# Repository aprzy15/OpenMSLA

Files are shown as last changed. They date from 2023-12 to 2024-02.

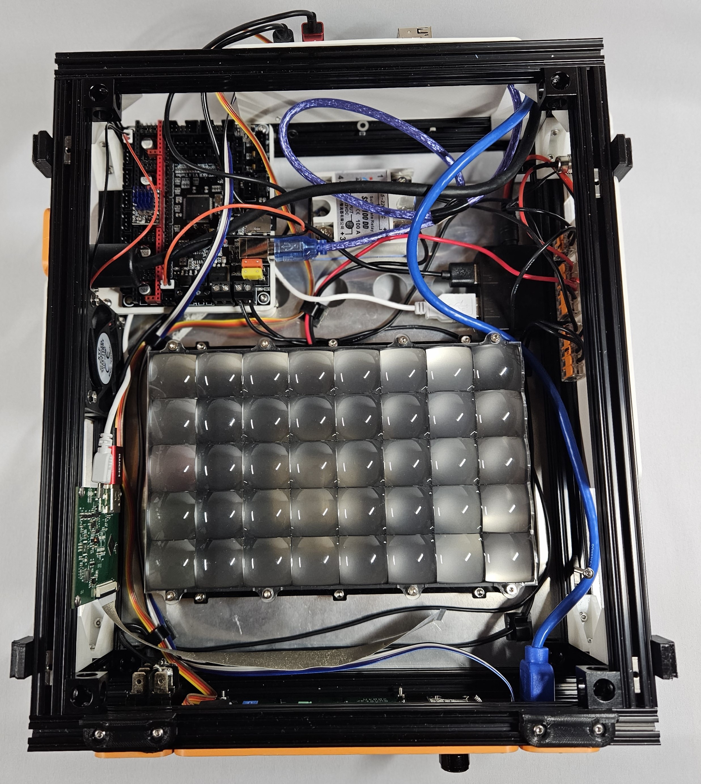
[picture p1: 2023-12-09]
hardware/photos/20231204_174026.jpg

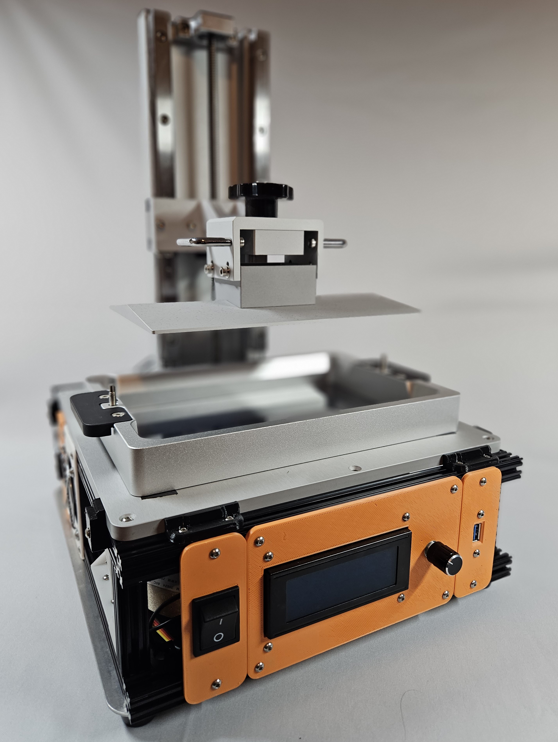
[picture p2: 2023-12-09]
hardware/photos/20231204_174818.jpg

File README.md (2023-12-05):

# OpenMSLA
Open-source resin 3D printer based on masked stereolithography (MSLA) technology

<p align="center" width="100%">
    
</p>

## Purpose

The purpose of the OpenMSLA project is to build an open-source, Python controlled 3D printer that provides operators with an extremely high level of control over printer operation.

## Why?

- As opposed to FDM 3D printing where there is a wide offering of open source 3D printers, almost all commercially available resin printers are closed source.
- Nearly all MSLA resin printers operate on a macro based architecture where machine parameters are defined on a layerwise basis and these parameters are duplicated for use in every subsequent layer.
  - This does not allow the operate to customize printing parameters beyond very basic settings.

## Objective

The objective of this project is to build a Gcode controlled resin printer that in principle will operate much more like an FDM 3D printer. Using this familiar interface should incentivize adoption and provide machine operators with an extremely high level of control over printing parameters of their printer.

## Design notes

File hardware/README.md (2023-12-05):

# Hardware Overview

### Donor Printer
The majority of the printer mechanical components are salvaged from a Phrozen Sonic Mighty 4K. At ~$400 the Sonic Mighty strikes a good balance between cost, quality and size. The LCD base plate, Z actuation arm, build plate, vat, and LED array are salvaged from the Sonic Mighty for use in this project. Unfortuately the LCD that comes with the Sonic mighty directly connects to the main control board via a MIPI cable. Due to the cloased source nature of the Phrozen control board running Chitubox firmware, reverse engineering the communication protocol between the board and the LCD mask would be a significant effort. The easier route is to purchase a new LCD mask off the shelf along with a dedicated LCD driver that allows for connection to a host PC over HDMI.

### Electrical Block Diagram

<p align="center" width="100%">
    
</p>

The OpenMSLA printer uses a Raspberry Pi which runs that main control software. The Pi interfaces with an SKR v1.4 Turbo control board running a flavor of Marlin to control the position of the Z axis actuator and the LCD driver board to display images to the LCD mask. The 24V LED curing array is controlled by a spare 5V fan PWM port on the SKR board via the solid state relay. The printer can be operated remotely over a local network or directly through the user interface mounted on the front of the printer which consists of a character LCD display and an encoder wheel for user input. One of the Pi's usb ports is exposed on the front panel to allow for insertion of a USB drive.

### TODO
- Covers need to be extended around the perimeter of the frame to prevent light bleed from the LED curing array.
- Make rear cover for the Raspberry Pi
- Cable management :)

<p align="center" width="100%">
    
</p>

<p align="center" width="100%">
    
</p>

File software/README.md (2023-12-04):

## OpenMSLA File Spec
The MSLA file is a zip folder with the .zip extension renamed to .msla
The MSLA file contains three main things:
- printconfig.ini file
- printplan.gcode file
- Collection of enumerated PNG files

### printconfig.ini
The print config file contains general information for the build: filename, number of layers, layer height, date time, material info, etc.
As of 11/18/2023 only the number of layers variable is actually used by the machine. The rest of the variables are mainly for record keeping purposes.

### printplan.gcode
The gcode file contains all of the commands for producing the build. This gcode is intended to be sent to a control board running Marlin. There are the following customizations to allow for the board to be used for resin printing purposes:
- ```M106 P0 S[0-255]```
	- The ```P0``` fan port is used to controller the solid state relay which controls power to the LED array. A value of 0 closes the relay, 255 opens the relay. Despite being a PWM port, this command can only be used to fully close or fully open the relay. Therefore only values of 0 and 255 should be used.
- ```M118 R1 I1```
		- ```M118``` is a standard Marlin M command that sends a serial message back to the host computer (in this case the Raspberry Pi). In this case the control board sends the command ```R1 I1``` back to the host. ```R``` Designates that this is a host command to be executed on the host computer. ```R1``` is the host command to display an image to the LCD. ```I1``` designates the index of the image to show. In this case the 1st image is displayed.
## OpenMSLA Gcode command architecture
An MSLA printer requires precise timing of image exposure and light exposure to accurately print parts. In the case of this machine, the image exposure is controlled by the host computer and timing of the LED array is controlled by the Gcode controller. This architecture necessitates precise timing between the host computer and Gcode controller.

When the Gcode controller is sent a Gcode command, this command is stored in an internal buffer until it is ready to be executed. When this internal buffer is filled the  controller will cease to accept new commands. This means that while the host computer knows precisely when a command is sent to the control board, it is "blind" as to when the command is actually executed. This introduces complications when trying to precisely time the display of layer to the LCD with the exposure by the LED array.

When Gcode controller is send a Gcode command, the host will wait until either a response is received or the timeout limit is reached. For most standard gcode commands the host waits for the ```ok``` response. For ```M118``` commands the host will wait for the specified serial message to be received, stalling the sending of gcode commands until this response is received.

The solution to this timing issue is to have the control board be the orchestrator during the print to control the timing of the LED array as well as the LCD. Because the LCD is controlled from the host computer this requires that the control board issue a command to the host computer when it wants a specific image to be displayed. Hence the ```M118 R1 I1``` command described above.

Based on these rules the typical layer is organized like the following:
```
G0 Z1 F500
M118 R1 I1
M400
M106 P0 S255
G4 P500
M106 P0 S0
```
- ```G0 Z1 F500``` Moves the Z axis to a specified Z height at a specified feed rate
	- This command is typically a set of multiple Z commands that control the peeling process and setting the next layer position
- ```M118 R1 I1``` This command issues the host command to display an image
- ```M400``` This command waits for all previously issues gcode commands to finish. In the case of long Z moves, this command is necessary to make sure the Z axis is in the correct position prior to turning on the LED array.
- ```M106 P0 S55``` Turns on the LED array
- ```G4 P500``` Is a 500ms dwell time. This dictates the curing time given for the resin
- ```M106 P0 S0``` Turns of the LED array
It is unclear what the actual timing of the LED array compared the designated dwell time. It is assumed that control board executes commands fast enough that the actual time the LED array is on it not significantly different from the commanded dwell time.

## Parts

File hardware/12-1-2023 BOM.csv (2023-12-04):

name | Manufacturer | vendor | package qty | order qty | price | total price | description | link
15x15x300mm Al extrusion | MakerBeam | MakerBeam | 4 | 3 | $12.36 | $37.08 | frame extrusion | https://www.makerbeam.com/openbeam-300mm-4p-black-openbeam.html
15x15x272mm Al extrusion | MakerBeam | MakerBeam | 4 | 1 | $14.39 | $14.39 | frame extrusion | https://www.makerbeam.com/openbeam-300mm-4p-black-openbeam.html
15x15mm t-slot nuts | MakerBeam | MakerBeam | 50 | 2 | $15.73 | $31.46 | frame t-slot nuts | https://www.makerbeam.com/t-slot-nuts-for-makerbeamxl-50p.html
15x15x60mm Al extrusion | MakerBeam | MakerBeam | 4 | 2 | $3.97 | $7.94 | frame extrusion | https://www.makerbeam.com/openbeam-60mm-4p-black-openbeam.html
15x15mm corner bracket | MakerBeam | MakerBeam | 12 | 1 | $19.47 | $19.47 | frame brackets | https://www.makerbeam.com/openbeam-corner-cubes-black-12p-for-makerbeamxl-or.html
SKR V1.4 Control Board | BIGTREETECH | Amazon | 1 | 1 | $44.99 | $44.99 | BIGTREETECH SKR V1.4 Turbo Control Board | https://www.amazon.com/dp/B082QR5YQ5?ref=ppx_yo2ov_dt_b_product_details&th=1
Raspberry Pi 4 | Raspberry Pi | Adafruit | 1 | 1 | $55.00 | $55.00 | Raspberry Pi 4 Model B - 4 GB RAM | https://www.adafruit.com/product/4296
Buck converter | DROK | Amazon | 1 | 1 | $12.99 | $12.99 | 12V to 5V DC-DC buck converter | https://www.amazon.com/dp/B07SS6XTZY?ref=ppx_yo2ov_dt_b_product_details&th=1
DC power jack | Lsgoodcare | Amazon | 20 | 1 | $13.99 | $13.99 | Panel pount DC input power jack | https://www.amazon.com/dp/B08LQ3SB3F?psc=1&ref=ppx_yo2ov_dt_b_product_details
Thermal pad | OwlTree | Amazon | 4 | 1 | $11.99 | $11.99 | Thermal conductive pad | https://www.amazon.com/dp/B096ZNHY8F?psc=1&ref=ppx_yo2ov_dt_b_product_details
USB panel mount | JUXNICE | Amazon | 2 | 1 | $12.99 | $12.99 | USB panel mount jack | https://www.amazon.com/dp/B09SQ7K7QP?ref=ppx_yo2ov_dt_b_product_details&th=1
Micro HDMI cable | Rulykar | Amazon | 1 | 1 | $23.99 | $23.99 | 1.5ft micro to standard HDMI cord | https://www.amazon.com/dp/B09P3GMFYX?ref=ppx_yo2ov_dt_b_product_details&th=1
SSR-100 | Jingzheng | Amazon | 1 | 1 | $18.12 | $18.12 | DC-DC solid state relay | https://www.amazon.com/dp/B08FHRT6GZ?psc=1&ref=ppx_yo2ov_dt_b_product_details
M3 metric screw kit | Kadrick | Amazon | 1290 | 1 | $23.97 | $23.97 | M3 button head machine screw kit | https://www.amazon.com/Kadrick-Aassortment-4mm-40mm-Commonly-Stainless/dp/B0BPFXP2M9?s=industrial
Sonic Mighty 4K | Phrozen | Phrozen | 1 | 1 | $409.99 | $409.99 | Phrozen Sonic Mighty 4K Resin 3D Printer | https://phrozen3d.com/products/sonic-mighty-4k
LCD mask | SUMAOPAI | AliExpress | 1 | 1 | $179.00 | $179.00 | 9.25in 6K Monochrome LCD | https://www.aliexpress.us/item/3256804234097190.html
LCD driver | SUMAOPAI | AliExpress | 1 | 1 | $45.00 | $45.00 | LCD driver board | https://www.aliexpress.us/item/3256804234097190.html

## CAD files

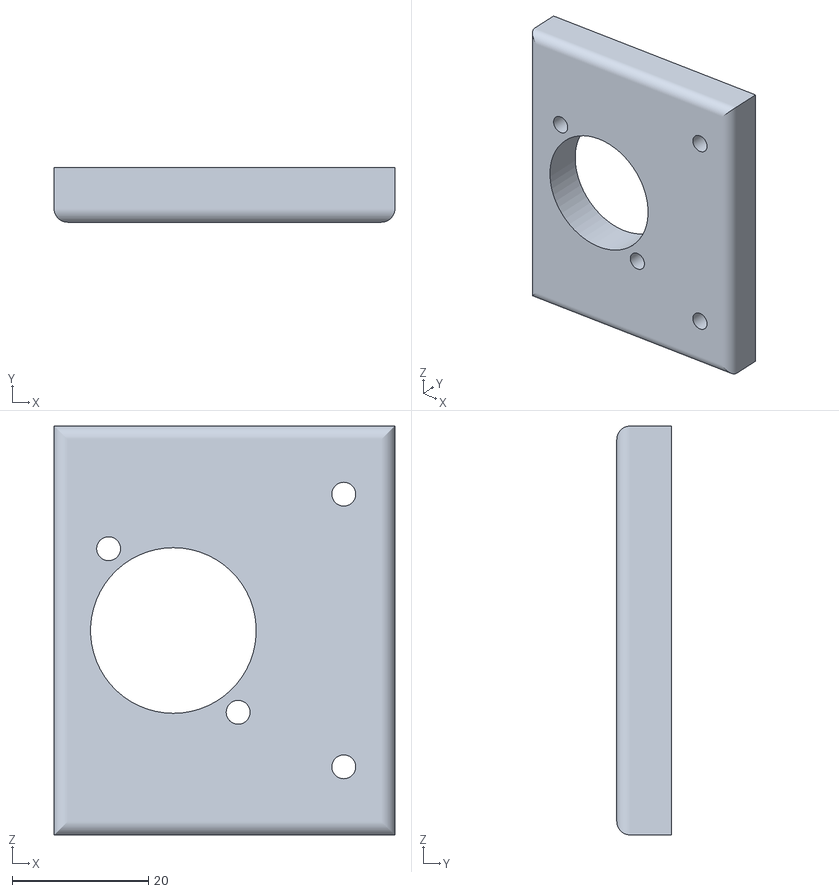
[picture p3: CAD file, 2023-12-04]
hardware/mechanical/CAD/STL/ethernet port bracket.stl
50.0 x 8.00 x 60.0

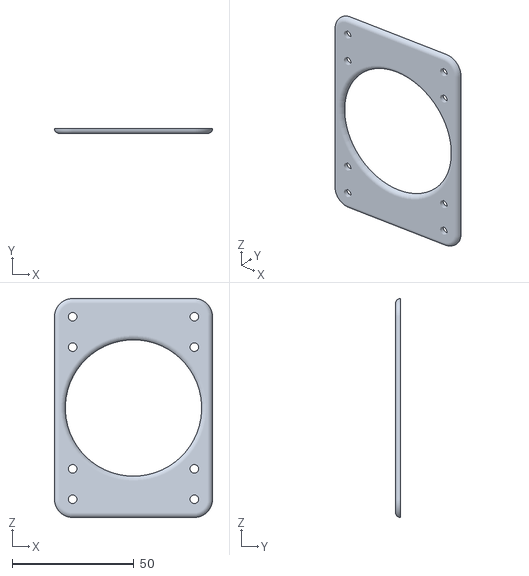
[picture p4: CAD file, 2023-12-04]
hardware/mechanical/CAD/STL/60mm fan bracket.stl
65.0 x 2.00 x 90.0

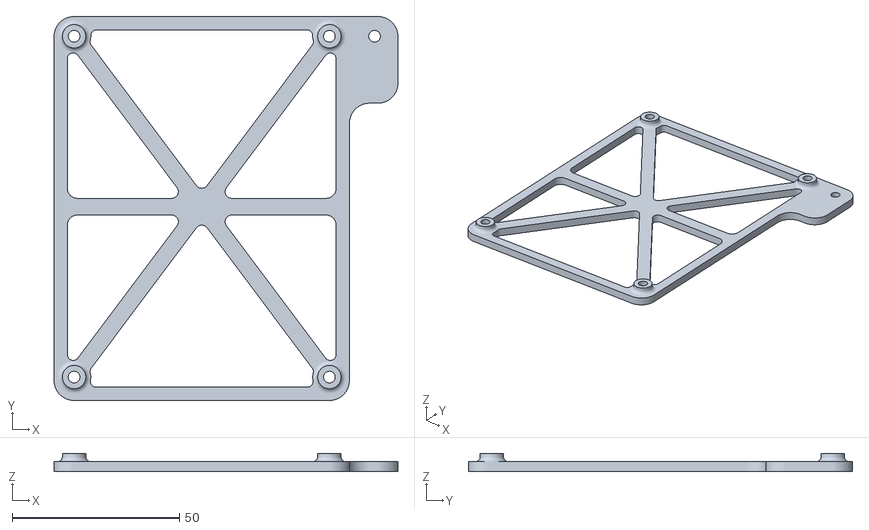
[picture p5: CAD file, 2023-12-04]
hardware/mechanical/CAD/STL/SKR bracket 1.stl
102.8 x 114.8 x 5.50

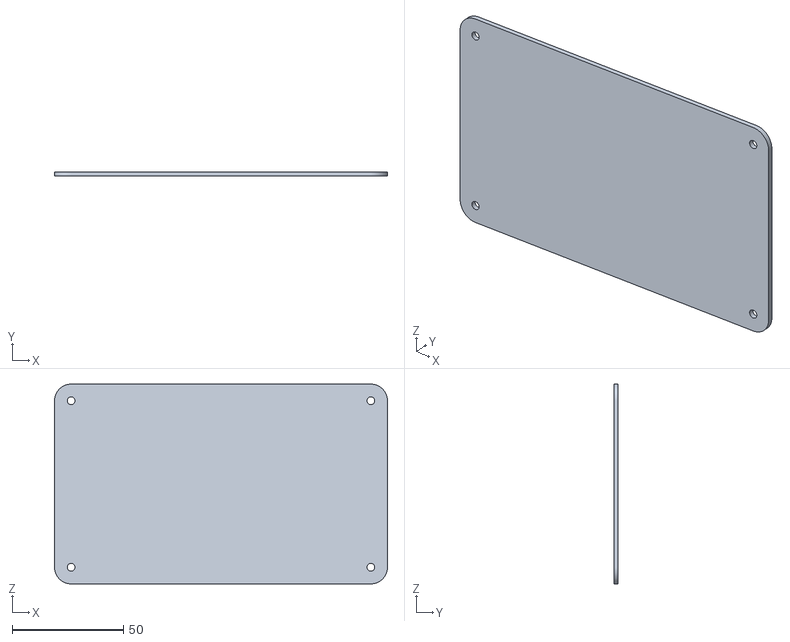
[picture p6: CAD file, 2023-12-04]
hardware/mechanical/CAD/STL/side panel wide.stl
150.0 x 2.00 x 90.0

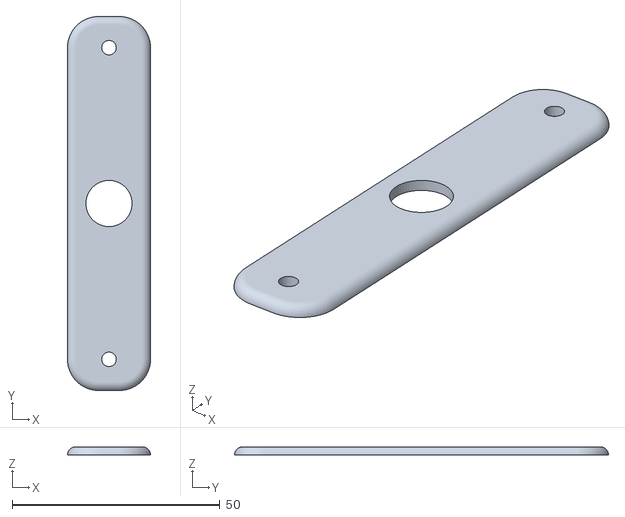
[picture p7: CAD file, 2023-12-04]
hardware/mechanical/CAD/STL/DC input plug bracket.stl
20.0 x 90.0 x 2.00

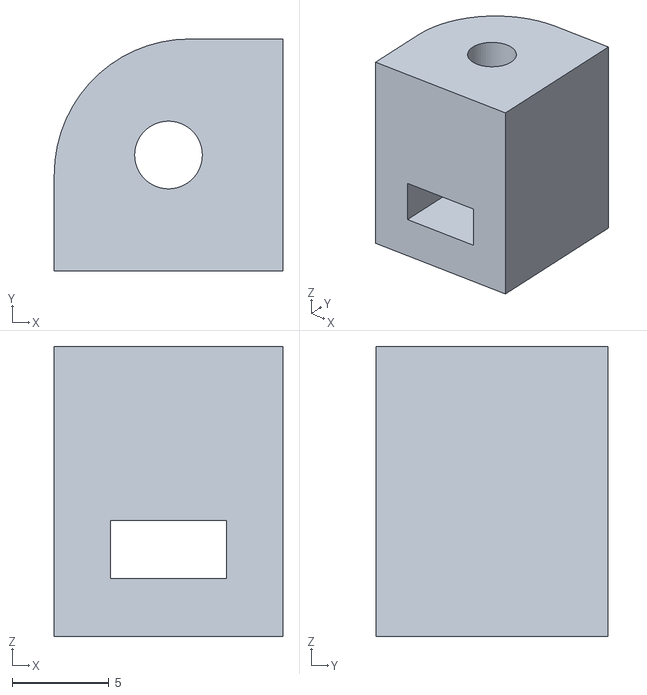
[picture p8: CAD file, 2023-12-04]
hardware/mechanical/CAD/STL/SKR standoff 2.stl
11.8 x 12.0 x 15.0

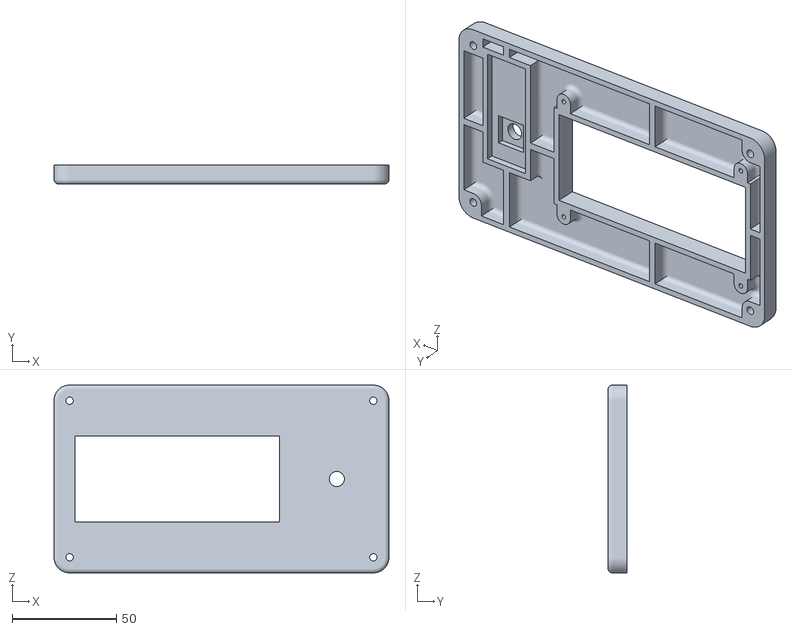
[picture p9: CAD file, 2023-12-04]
hardware/mechanical/CAD/STL/ui_lcd_bracket.stl
160.5 x 9.00 x 90.0

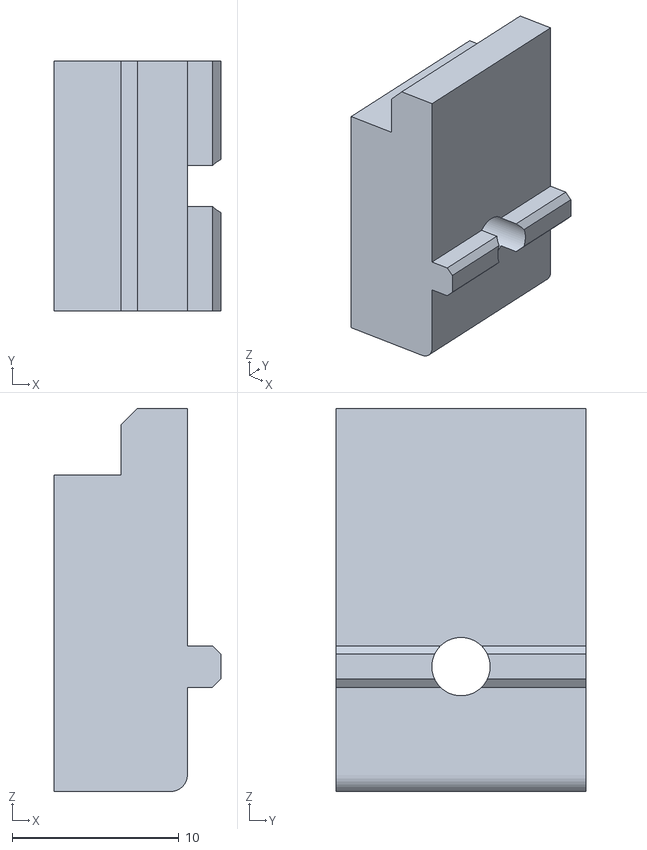
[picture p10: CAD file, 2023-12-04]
hardware/mechanical/CAD/STL/cover mount side.stl
10.0 x 15.0 x 23.0

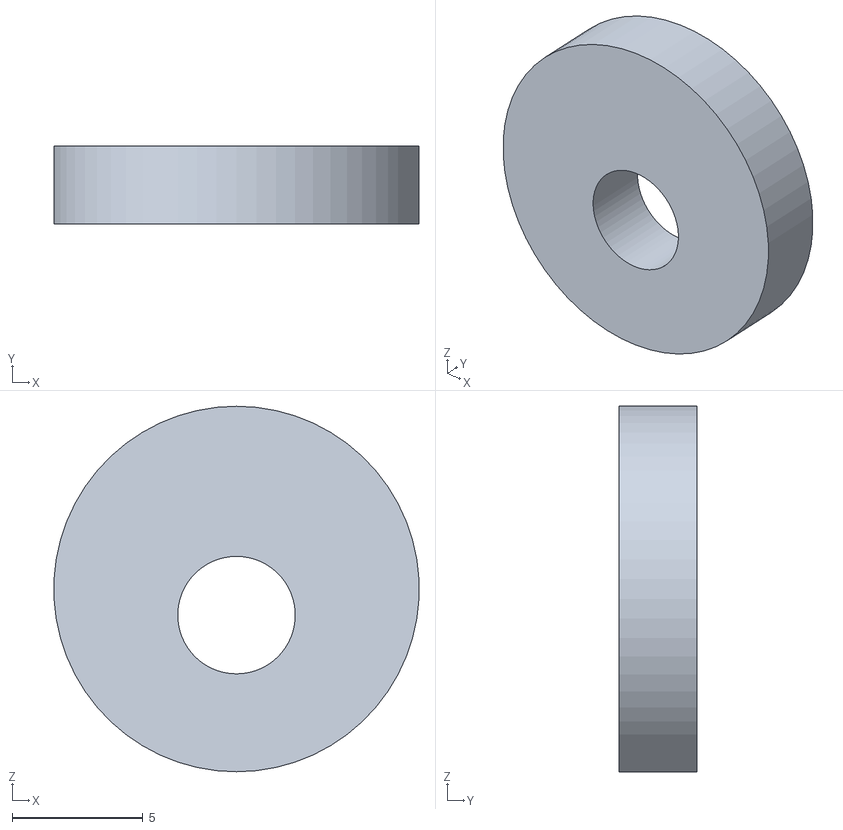
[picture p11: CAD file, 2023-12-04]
hardware/mechanical/CAD/STL/cover mount back.stl
14.0 x 3.00 x 14.0

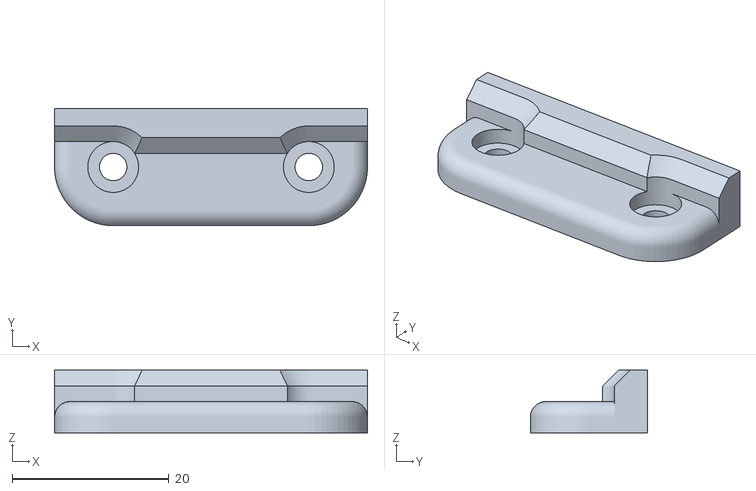
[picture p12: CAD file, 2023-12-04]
hardware/mechanical/CAD/STL/cover mount front.stl
40.0 x 15.0 x 8.00

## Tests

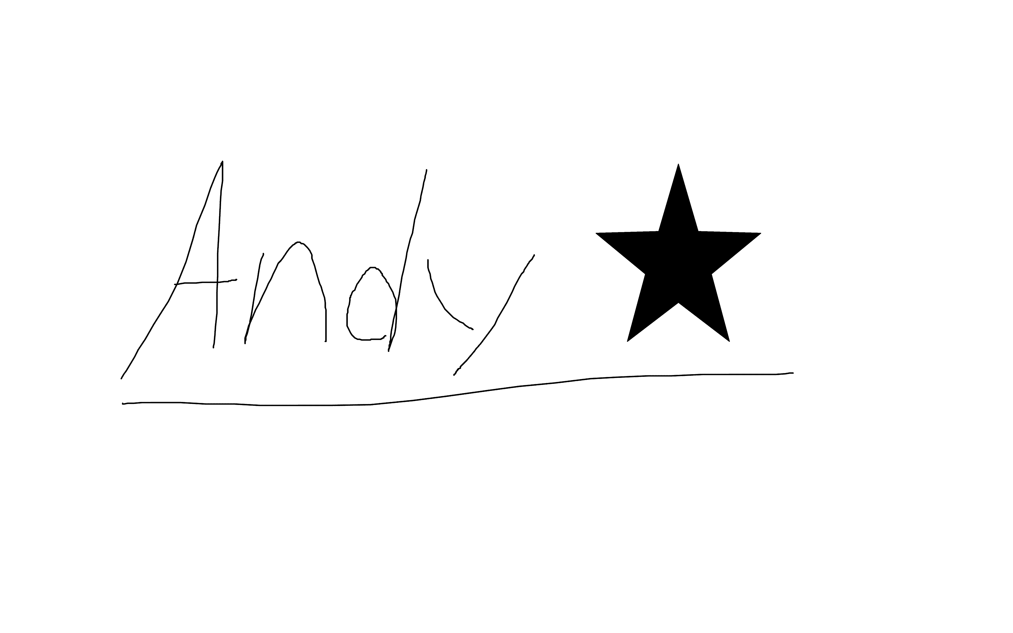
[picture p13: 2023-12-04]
software/tests/LCD_test_im.png

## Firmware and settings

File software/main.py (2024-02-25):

from printer import Printer
from controller_ui import UiController
import os
from multiprocessing import Process
from pubsub import pub
from config.config_machine import MachineConfig


def headless(cfg):
    printer = Printer(cfg)
    # fpath = os.path.join('test_files', 'test-print')
    # fpath = r'/home/admin/printer/software/test_files/test-print'
    fpath = cfg.headless_filepath
    printer.start_print(fpath)


def with_ui(cfg):
    printer = Printer(cfg)
    UiController(cfg)


if __name__ == '__main__':
    cfg_path = r'/home/admin/printer/software/config/machine_config.json'
    cfg = MachineConfig(cfg_path)
    if cfg.run_headless:
        headless(cfg)
    else:
        with_ui(cfg)
    # printer = Printer(cfg)
    # UiController(cfg)

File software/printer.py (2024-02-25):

from controller_gcode import GcodeController, GcodeCommand
from config.config_machine import MachineConfig
from pubsub import pub
from controller_display import Display
from print_file import PrintData
import time


class Printer:
    def __init__(self, cfg):
        # pub.subscribe(self.home_z, 'printer.home')
        self.cancel_flag = False
        self.archive = None
        self.cfg = cfg
        self.controller = GcodeController(self.cfg)
        self.display = Display(self.cfg)
        self.init_pubsub()
        print('Printer Initialized')

    def init_pubsub(self):
        pub.subscribe(self.controller.move_z, 'ui.z_changed')
        pub.subscribe(self.controller.home, 'printer.home')
        # pub.subscribe(self.home_z, 'printer.home')
        pub.subscribe(self.start_print, 'printer.start_print')
        pub.subscribe(self.cancel_print, 'printer.cancel_print')
        pub.subscribe(self.start_macro, 'printer.start_macro')

    def home_z(self):
        print('home z host')
        self.controller.home()

    def start_print(self, fpath):
        print_file = PrintData(fpath)
        if not print_file.exists:
            print('File does not exist')
            pub.sendMessage('ui.print_end')
            return
        pub.sendMessage('ui.print_info', print_layers=print_file.cfg.num_layers, fname=print_file.cfg.file_name)
        # Read Gcode file
        gcode_commands = print_file.gcode_commands
        # Loop through gcode commands
        self.cancel_flag = False
        for gcode_str in gcode_commands:
            if self.cancel_flag:
                break
            command = GcodeCommand(gcode_str)
            response = self.controller.execute(command)
            if command.is_host_command:
                self.parse_host_command(response, print_file)
        command = GcodeCommand("M106 P0 S0\r\n")
        response = self.controller.execute(command)
        pub.sendMessage('ui.print_end')

    def cancel_print(self):
        self.cancel_flag = True

    def start_macro(self, fpath):
        f = open(fpath)
        gcode = f.readlines()
        for raw_command in gcode:
            command = GcodeCommand(raw_command)
            self.controller.execute(command)

    def parse_host_command(self, cmd_str, print_file):
        if cmd_str.startswith('R1 '):
            self.R1(cmd_str, print_file)

    def R1(self, command, print_file):
        # Show image
        parts = command.rstrip('\r').strip(' ').split(' ')
        index = int(parts[1].lstrip('I'))
        pub.sendMessage('ui.layer_start', current_layer=index)
        img = print_file.get_image(index)
        res = self.display.show(img)
        time.sleep(0.2)  # Only needed if move command is really quick


if __name__ == '__main__':
    cfg_path = r'./config/machine_config.json'
    printer = Printer(cfg_path)

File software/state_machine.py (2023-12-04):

import os
from pubsub import pub
import numpy as np
import subprocess
import json
import logging

def find_drive(d, target):
    devices = d['blockdevices']
    for device in devices:
        children = device['children']
        for child in children:
            name = child['name']
            label = child['label']
            if label == target:
                return name
    return None



class StateMachine:
    def __init__(self, cfg, lcd):
        self.state = None
        self.macros = []
        self.fname = ''
        self.current_layer = 0
        self.max_layer = 1
        self.is_changed = False
        self.is_homed = False
        self.z_pos = 0
        self.files = []
        self.cfg = cfg
        self.lcd = lcd
        self.navigate(MainPage)

    def navigate(self, class_obj):
        self.state = class_obj(self)
        self.state.update_screen()

    def load_files(self):
        self.files = []
        res = subprocess.check_output(f"lsblk -o name,label --json", shell=True).decode()
        d = json.loads(res)
        # TODO search dictionary for thumb label, return device name
        label = 'thumb'
        port = find_drive(d, label)
        if port is None:
            print(f'Error: Cannot locate drive label: {label}')
            return
        os.system(f"sudo mount -t exfat /dev/{port} /home/usbdrive")
        raw_files = os.listdir(self.cfg.build_folder)
        print(raw_files)
        for file in raw_files:
            if os.path.splitext(file)[1] == self.cfg.file_ext:
                self.files.append(file)
            elif os.path.splitext(file)[1] == '.gcode':
                self.macros.append(file)


class AbstractPage:
    def __init__(self):
        pass

    def update_screen(self):
        pass

    def enter(self):
        pass

    def up(self):
        pass

    def dn(self):
        pass


class GenericListPage:
    def __init__(self, context, page_list):
        self.lcd = context.lcd
        self.nrows = context.cfg.lcd_rows
        self.context = context
        self.wind_start_index = 0
        self.last_cur_index = 0
        self.cur_index = 0
        self.last_index = 0
        self.page_list = page_list
        # self.update_screen()

    def update(self, index):
        if index == self.last_index:
            return
        self.last_index = index
        if self.cur_index == self.last_cur_index:
            self.wind_start_index = max([0, index - (self.nrows - 1)])
            self.update_screen()
        else:
            self.update_cursor()

    def update_screen(self):
        pages = self.page_list[self.wind_start_index:self.wind_start_index + self.nrows]
        str_list = []
        for i, page in enumerate(pages):
            name = page['name']
            str_list.append(' ' + name)
        screen = '\r\n'.join(str_list)
        self.lcd.clear()
        self.lcd.write_string(screen)
        self.update_cursor()

    def update_cursor(self):
        self.lcd._set_cursor_pos((self.last_cur_index, 0))
        self.lcd.write_string(' ')
        self.lcd._set_cursor_pos((self.cur_index, 0))
        self.lcd.write_string('>')
        self.last_cur_index = self.cur_index

    def enter(self):
        d = self.page_list[self.last_index]
        page = d['page']
        self.context.navigate(page)

    def up(self):
        self.cur_index = max([0, self.last_cur_index - 1])
        index = max([0, self.last_index - 1])
        self.update(index)

    def dn(self):
        self.cur_index = min([self.nrows - 1, self.last_cur_index + 1])
        index = min([len(self.page_list) - 1, self.last_index + 1])
        self.update(index)


class MainPage(GenericListPage):
    def __init__(self, context):
        page_list = [
            {'name': 'Info', 'page': ZAdjust},
            {'name': 'Adjust Z', 'page': ZAdjust},
            {'name': 'Load Files', 'page': FilePage},
            {'name': 'Home Z', 'page': HomePage},
            {'name': 'Macros', 'page': MacroPage},
        ]
        super().__init__(context, page_list)


class FilePage(GenericListPage):
    def __init__(self, context):
        print(self.__repr__())
        context.load_files()
        files = context.files.copy()
        page_list = []
        for file in files:
            name = file
            if len(file) > context.cfg.lcd_cols:
                name = file[:context.cfg.lcd_cols-1]
            d = {'name': name, 'file': file, 'page': PrintingPage}
            page_list.append(d)
        page_list.append({'name': 'Back', 'file': None, 'page': MainPage})
        super().__init__(context, page_list)

    def enter(self):
        d = self.page_list[self.last_index]
        page = d['page']
        file = d['file']
        self.context.navigate(page)
        if file is not None:
            self.context.fname = file
            fpath = os.path.join(self.context.cfg.build_folder, file)
            pub.sendMessage('start_print', fpath=fpath)


class MacroPage(GenericListPage):
    def __init__(self, context):
        context.load_files()
        macros = context.macros.copy()
        page_list = []
        for macro in macros:
            name = macro
            if len(macro) > context.cfg.lcd_cols:
                name = macro[:context.cfg.lcd_cols-1]
            d = {'name': name, 'file': macro, 'page': PrintingPage}
            page_list.append(d)
        page_list.append({'name': 'Back', 'file': None,'page': MainPage})
        super().__init__(context, page_list)

    def enter(self):
        d = self.page_list[self.last_index]
        page = d['page']
        file = d['file']
        self.context.fname = file
        if file is not None:
            self.context.navigate(page)
            fpath = os.path.join(self.context.cfg.build_folder, file)
            pub.sendMessage('start_macro', fpath=fpath)


class PrintingPage(AbstractPage):
    def __init__(self, context):
        print(self.__repr__())
        super().__init__()
        self.lcd = context.lcd
        self.current_layer = 0
        self.context = context

    def update_screen(self):
        max_layer = self.context.max_layer
        layer_str = f'{self.context.current_layer} / {max_layer}'
        num_bars = np.round((self.context.current_layer / max_layer) * self.context.cfg.lcd_cols).astype(int)
        percent_complete = ''.join(["\xff"] * num_bars)
        text = '\r\n'.join(['Printing', self.context.fname, layer_str, percent_complete])
        self.lcd.clear()
        self.lcd.write_string(text)

    def enter(self):
        self.context.navigate(CancelPage)
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

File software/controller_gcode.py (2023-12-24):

import serial
import time
from pubsub import pub


class GcodeCommand:
    def __init__(self, command):
        self.raw_string = command
        parts = command.rstrip('\n').split(' ')
        self.is_host_command = False
        self.response_code = 'ok'
        if command.startswith('M118 '):
            self.response_code = parts[1]
            self.is_host_command = True
        elif command.startswith('G28 '):
            self.response_code = 'X'


class GcodeController:
    def __init__(self, cfg):
        self.serial = None
        self.cfg = cfg
        self.commands = []
        self.init_controller()

    def init_controller(self):
        self.serial = serial.Serial(self.cfg.controller_port, 115200)
        time.sleep(1)
        self.serial.reset_input_buffer()
        time.sleep(0.6)
        self.send("M501\n")
        self.send(f"M92 Z{self.cfg.steps_mm}\n")
        self.send("M500\n")
        self.send("M211 S0\n")
        time.sleep(0.5)
        self._wait_for_gcode_response('ok', 20)

    def execute(self, command, timeout=60):
        self.send(command.raw_string)
        response = self._wait_for_gcode_response(command.response_code, timeout)
        return response
        # if command.is_host_command:
        #     return response
        # else:
        #     if response:
        #         return True
        #     else:
        #         return False

    def home(self):
        print('homing')
        command = GcodeCommand(f"G28 Z\r\n")
        status = self.execute(command)
        pub.sendMessage('homing_status', status=status)

    def move_z(self, arg1):
        print(f'move Z {arg1}')
        command = GcodeCommand(f"G0 Z{arg1} F1000\n")
        self.execute(command)

    def send(self, gcode_string):
        self.serial.write(str.encode(gcode_string))

    def read(self):
        return self.serial.read_until().decode('ascii').rstrip('\n')

    def _wait_for_gcode_response(self, response_code, timeout):
        res = self.read()
        t0 = time.time()
        while not res.startswith(response_code):
            time.sleep(0.25)
            res = self.read().strip(' ')
            if time.time() - t0 > timeout:
                print('COMMAND TIMEOUT ERROR')
                return None
        return res

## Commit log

2023-12-22 Updated USB drive reading process
    switched to using USBmount package instead of manually remounting usb drives every time
    [machine_config.json]
2023-12-24 refactor + fixed lcd driver
    [machine_config.json]
2024-02-25 added headless run spec to config file
    also fixed a bug with the layer number not resetting after a print
    [machine_config.json]
